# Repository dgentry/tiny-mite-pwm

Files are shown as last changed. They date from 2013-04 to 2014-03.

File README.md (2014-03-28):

TinyMite PWM
=============

A small, cheap, programmable PWM controller suitable for driving
LEDs or motors.  Based on 8 pin ATTiny uControllers.

What good is it?  Features:
* Compact (1" x 1.25")
* Can drive two paralleled MOSFETs
* Can take a kickback suppression (flywheel) diode for driving motors or solenoids.
* Programmable since it's based on an AtTiny microcontroller (ATTiny 25, 45, 85, and probably 13 all work).
* Has space for a couple of programmable status LEDs
* Capable of input from a switch or potentiometer
* Can monitor a thermistor for high temperature protection

Choose your MOSFET(s), and if you're driving a
motor, your kickback diode, and have at it.

I have built it with various MOSFETS and kickback diodes, but a good
combination seems to be an IRF2804 (42 volt, 270 amp) and On Semi MBR30H150
(30 amp, 150 volt dual Schottky in a TO-220 package), where it happily
controls a 25 amp fan motor in my Crown Victoria.  In that
application, it's on the edge of needing heat sinks.

A note on PWM and component choices
-----------------------------------
Here's what I have learned about MOSFETs and kickback diodes.

IRF2804s cost something like $3.00 these days, so maybe there's
something newer, better and cheaper (the IRFZ44N looks good to me at
$1.18 each for 10 from Newark).  The parameters to pay attention to
are:
* I_d (Continuous Drain current)
* V_ds (Drain Source voltage), and
* R_dson (On Resistance) at the manufacturer's rated test voltage.

I choose I_d to be at least twice the (fuse) rating of the motor, but
with LEDs you could probably get away with something just above the
total load current.  The IRFZ44 is only rated at 49 amps (vs. 270 amps
for the IRF2804), but that should be OK (with a heatsink) for my 25
amp fan motor.

V_ds must be well above the maximum transient voltage spike you ever
expect, since MOSFETs can instantly fail if you exceed that voltage,
even for a moment.  In a car (nominally 13.6 volts), Automotive rated
MOSFETS like the IRF2804 or the IRFZ44N should be fine, and they have
Vgs ratings of 42 and 55 volts, respectively.

R_dson primarily determines one source of power (heat) you'll have to
dissipate from your MOSFET.  Automotive MOSFETs (in particular, the
IRF2804) have amazingly low R_dson, so they can have crazily high I_d
ratings (270 amps continuous), limited only by the TO-220 packaging.
Power is I^2 * R, so 25 amps * 2.3 mOhm = 1.5 watts, which technically
requires a heatsink above ~ 50 degrees C ambient, but my car interior
doesn't stay at 50 degrees C when I'm running the A/C + fan.

The other source of heat is switching losses -- every time the PWM
changes from high to low or the other way around, for a very brief
period (and we make it as brief as possible, in the microseconds
range) some current is flowing through the MOSFET with moderate
resistance.  At lower switching frequencies (say 1 khz to 10 khz), the
several microseconds switching time is negligible compared to the
pulse width (1 millisecond to 100 microseconds).  As the frequencies
get higher (say 20 khz to 100khz giving 50 microsecond to 10
microsecond pulses), the switching time is a significant fraction of
the pulse width, so you have to pay attention to the heat generated
then.  I haven't noticed any whine from my motor or circuit (it's in a
noisy car, after all), so switching at 2 khz doesn't add much in the
way of switching losses, while the motor still "sees" relatively
smooth power.

Datasheets
----------
IRF2804:  http://www.irf.com/product-info/datasheets/data/irf2804.pdf
http://www.newark.com/international-rectifier/irf2804pbf/n-ch-mosfet-40v-270a-to-220ab/dp/63J7214

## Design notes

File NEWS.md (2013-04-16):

Fixed
-----

* the PWM output from the atTiny is at 5 volts, so the totem pole
  output is only driven between 0 and 5v instead of the full voltage
  input range.  [fixed 2013-04-15]

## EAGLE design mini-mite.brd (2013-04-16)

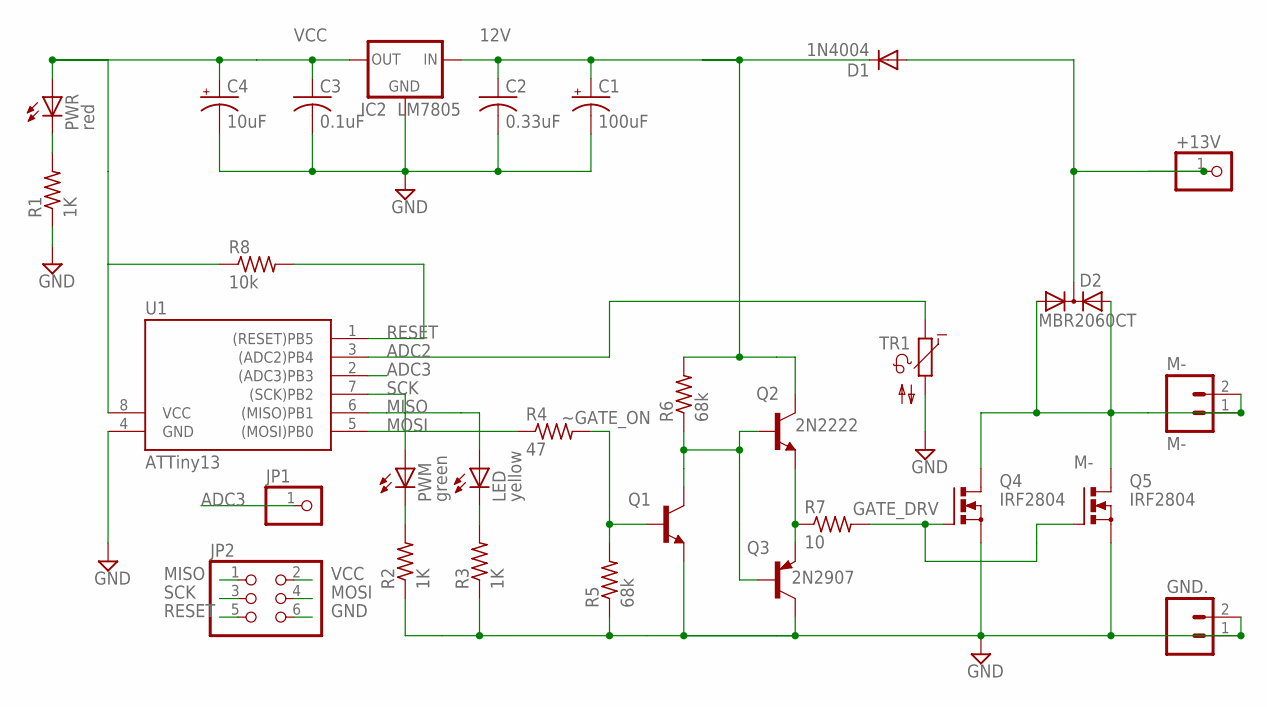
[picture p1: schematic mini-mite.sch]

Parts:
+13V: 1X01
C1: 100uF; E2,5-6
C2: 0.33uF; C025-025X050
C3: 0.1uF; C025-025X050
C4: 10uF; E2,5-6
D1: 1N4004; DO41-10
D2: MBR2060CT; TO220ABS
GND.: M02LOCK_LONGPADS; 1X02_LOCK_LONGPADS
IC2: LM7805; 78XXS
JP1: PINHD-1X1; 1X01
JP2: PINHD-2X3; 2X03
LED: yellow; LED5MM
M-: M-; 1X02_LOCK_LONGPADS
PWM: green; LED5MM
PWR: red; LED5MM
Q1, Q2: 2N2222; TO92-EBC-OVAL
Q3: 2N2907; TO92-EBC-OVAL
Q4, Q5: IRF2804; TO220BV
R1, R2, R3: 1K; 0207/7
R4: 47; 0207/10
R5, R6: 68k; 0207/7
R7: 10; 0207/7
R8: 10k; 0207/7
TR1: NTC642-6; P642
U1: ATTiny13; DIL08

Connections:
12V: C1.+, C2.1, D1.C, IC2.IN, Q2.C, R6.2
+13V: +13V.1, D1.A, D2.C
ADC2: TR1.1, U1.3 ((ADC2)PB4)
ADC3: JP1.1, U1.2 ((ADC3)PB3)
GATEON: Q1.C, Q2.B, Q3.B, R6.1
GATE_DRV: Q4.G, Q5.G, R7.2
GND: C1.-, C2.2, C3.2, C4.-, GND..1, GND..2, IC2.GND, JP2.6, Q1.E, Q3.C, Q4.S, Q5.S, R1.1, R2.1, R3.1, R5.1, TR1.2, U1.4 (GND)
M-: D2.A1, D2.A2, M-.1, M-.2, Q4.D, Q5.D
MISO: JP2.1, LED.A, U1.6 ((MISO)PB1)
MOSI: JP2.4, R4.1, U1.5 ((MOSI)PB0)
unnamed: LED.K (C), R3.2
unnamed: Q2.E, Q3.E, R7.1
unnamed: PWR.K (C), R1.2
unnamed: PWM.K (C), R2.2
RESET: JP2.5, R8.2, U1.1 ((RESET)PB5)
SCK: JP2.3, PWM.A, U1.7 ((SCK)PB2)
VCC: C3.1, C4.+, IC2.OUT, JP2.2, PWR.A, R8.1, U1.8 (VCC)
~GATE_ON: Q1.B, R4.2, R5.2

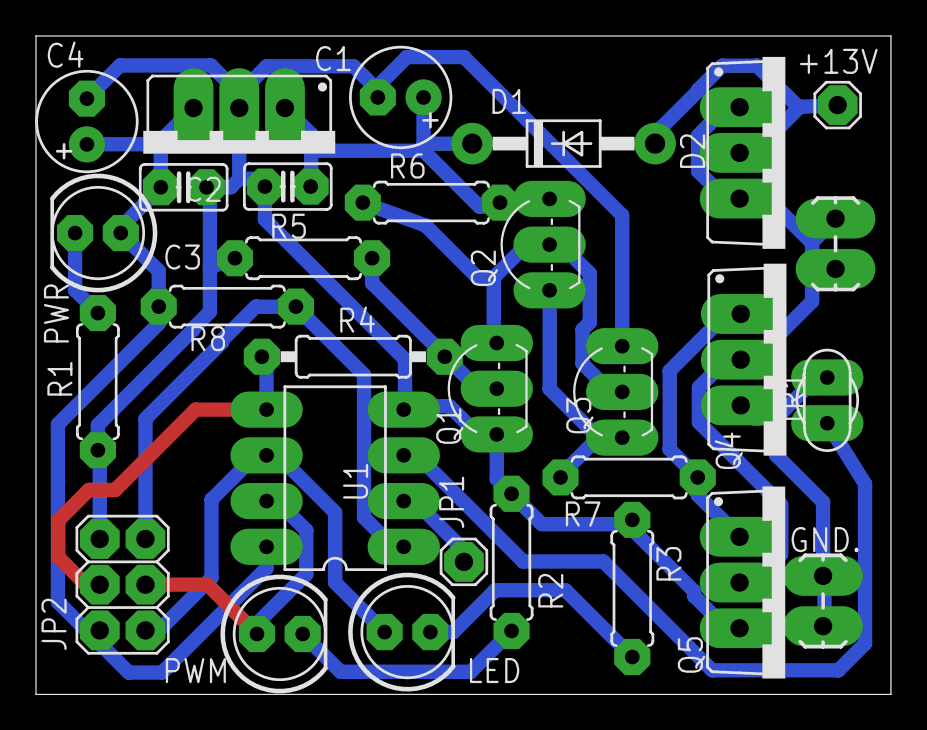
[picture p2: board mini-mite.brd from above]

Board: 2 copper layers, 47.5 x 36.6 mm, 30 parts (0 on the bottom side), 18 nets.

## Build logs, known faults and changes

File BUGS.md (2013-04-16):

Bugs
----

* I haven't proved that the internal pullup resistor is sufficient for
  making a voltage divider with my thermistor, so we might need to add
  an external resistor.

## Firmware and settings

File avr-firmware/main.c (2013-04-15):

/* Name: main.c
 * Author: Dennis Gentry
 * Copyright 2010, Dennis Gentry
 * License: Creative Commons Attribution
 */

/* 
 * Title: PWM for the Neophyte
 * Hardware: ATtiny13
 */
 
//#define F_CPU 9600000UL // Define software reference clock for delay duration
#include <stdlib.h>
#include <avr/io.h>
#include <util/delay.h>
#include <assert.h>


// For hardware PWM, only PB0 or PB1 have timer/counter support
#define PWM_OUT_PIN PB0

#define LED PB2
#define POT PB3  // (aka ADC3)
#define GATE PB1  // The gate of the MOSFETs we want to control
#define TEMP PB4  // (ADC 2) The Thermistor (other leg is grounded)

unsigned char duty_cycle;  // In the 0 - 255 range
#define MIN_DUTY_CYCLE 0
#define MAX_DUTY_CYCLE 255

void mydelay(int ms);
void flash_number(int num);
void flash_number_in_binary(unsigned char num);
unsigned char a_to_d(unsigned char pin);

/* Making variables static for ISRs */

unsigned char temperature;

int main (void)
{
  DDRB |= (1 << LED); // Make LED an output, Will want to blink LED
  DDRB |= (1 << GATE); // Make GATE an output
  DDRB &= ~(1 << TEMP);

  /* Set up to read Pot */
  DDRB &= ~(1<< POT); // Set POT as an input (0-5v)
  ADCSRA |= (1 << ADEN)| // Analog-Digital enable bit
    (1 << ADPS1)| // set prescaler to 8 (clock / 8)
    (1 << ADPS0); // set prescaler to 8 (clock / 8)
 

  /* Set up PWM */
  //DDRB |= (1 << PWM_OUT_PIN); // OC0A on PB0
  // COM0A1 - COM0A0 (Set OC0A on Compare Match, clear OC0A at TOP)
  //TCCR0A |= ((1 << COM0A1) | (1 << COM0A0) 
  //	     | (1 << WGM01) | (1 << WGM00)); // WGM01 - WGM00 (set fast PWM)
  //OCR0A = 0; // initialize Output Compare Register A to 0

  //TCCR0B |= (1 << CS01); // Start timer at Fcpu / 256
 

  flash_number_in_binary(0);
  flash_number_in_binary(TEMP);
  flash_number_in_binary(15);
  flash_number_in_binary(POT);

  while (1) {

    // Sample POT to get desired motor speed
    duty_cycle = a_to_d(POT);

    //----------Show ADCH Byte in Led variable brightness indicator---------
 
    if (duty_cycle > 0) {
      PORTB |= (1 << LED);  // Turn on the LED
      PORTB |= (1 << GATE); // and the MOSFETs
    }
    mydelay(duty_cycle);

    // Sample
    temperature = a_to_d(TEMP); //(100K/4.7K thermistor/resistor
			// ~5v - .2v, ~4.1v = 60C, ~2.5v = 100C)

    if (temperature > ((4.5/5.0)*256)) {
      flash_number_in_binary(temperature/32);
    }

    if (duty_cycle < MAX_DUTY_CYCLE) {
      PORTB &= ~(1 << LED);   // Turn off the LED
      PORTB &= ~(1 << GATE);  // and the MOSFETs
    }
    mydelay(MAX_DUTY_CYCLE - duty_cycle);

  }
  return 0; // not reached
}

unsigned char a_to_d(unsigned char pin) 
{
  unsigned char mux = 0;  //(ADC0/PB5 = 00, ADC1/PB2 = 01, ADC2/PB4 = 10, ADC3/PB3 = 11)

  flash_number_in_binary(pin);
  if (pin == PB2) mux = 1;
  else if (pin == PB4) mux = 2;
  else if (pin == PB3) mux = 3;


  ADMUX |= (1 << ADLAR)| // AD result store in (most significant bit in ADCH)
    (mux & ((1 << MUX1) | (1 << MUX0))); // Choose AD input 

  // ADMUX should be 0b001000mm where mm is the mux value
  assert(ADMUX >= 0b00100000 && ADMUX <= 0b00100011);

  flash_number_in_binary(ADMUX);

  ADCSRA |= (1 << ADEN); // Analog-Digital enable bit
  ADCSRA |= (1 << ADSC); // Discard first conversion

  while (ADCSRA & (1 << ADSC)); // wait until conversion is done
    
  ADCSRA |= (1 << ADSC); // start another conversion
 
  while (ADCSRA & (1 << ADSC)); // wait until conversion is done
 
  ADCSRA &= ~(1<<ADEN); // shut down the ADC

  return ADCH;
}
 
 
/*
 *  Flash LED <num> times, then pause.
 */
void flash_number(int num)
{
  int i;
  for (i = 0; i < 4; i++) {
    _delay_ms(50);
  }

  for (i = 0; i < num; i++) {
    PORTB |= (1 << LED);
    _delay_ms(15);
    PORTB ^= (1 << LED); // Invert led bit and show it
    _delay_ms(45);
  }


  for (i = 0; i < 4; i++) {
    _delay_ms(50);
  }
}



/*
 *  Flash <num> in binary on the LED
 */
void flash_number_in_binary(unsigned char num)
{
  char i, j;  // Really only need 4 bits for each of these -- bit pointers into a byte

  for (i = 0; i < 4; i++) {
    _delay_ms(50);
  }

  // Find first set bit (isn't there a libc function for this?)
  for (i = 7; i >= 0 && !(num & (1 << i)); i--);
  // i either points at the first set bit, or -1

  // Always flash at least bits 3 - 0
  if (i<3) i = 3;


  for (j = i; j >= 0; j--) {
    PORTB |= (1 << LED);  // Flame on
    if (num & (1 << j)) {
      _delay_ms(60);
      PORTB &= ~(1 << LED); // Flame off
    } else {
      _delay_ms(10);
      PORTB &= ~(1 << LED); // Flame off
      _delay_ms(50);
    }

    _delay_ms(40);
  }

  for (i = 0; i < 4; i++) {
    _delay_ms(50);
  }
}




void mydelay(int ms)
{
  int i;

  for (i = 0; i < ms; i++) {
    _delay_us(5);
  }
}

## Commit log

2013-04-15 Populate the repo.
    [mini-mite.brd, mini-mite.sch]
2013-04-16 Fixed drive voltage range bug.
    [mini-mite.brd, mini-mite.sch]

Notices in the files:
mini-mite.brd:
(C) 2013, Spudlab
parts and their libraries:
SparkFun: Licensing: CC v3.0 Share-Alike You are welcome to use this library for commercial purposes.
